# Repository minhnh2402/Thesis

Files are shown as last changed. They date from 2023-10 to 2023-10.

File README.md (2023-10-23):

# THIẾT KẾ VÀ ĐIỀU KHIỂN ROBOT DELTA CỘNG TÁC VỚI CON NGƯỜI

- [THIẾT KẾ VÀ ĐIỀU KHIỂN ROBOT DELTA CỘNG TÁC VỚI CON NGƯỜI](#thiết-kế-và-điều-khiển-robot-delta-cộng-tác-với-con-người)
  - [1. Mục tiêu đồ án](#1-mục-tiêu-đồ-án)
  - [2. Thiết kế cơ khí](#2-thiết-kế-cơ-khí)
  - [3. Thiết kế hệ thống điện](#3-thiết-kế-hệ-thống-điện)
  - [4. Mô hình hoá và thiết kế bộ điều khiển](#4-mô-hình-hoá-và-thiết-kế-bộ-điều-khiển)
  - [5. Xây dựng chương trình điều khiển Robot](#5-xây-dựng-chương-trình-điều-khiển-robot)
    - [5.1. Điều khiển robot thông qua mạng RTEX](#51-điều-khiển-robot-thông-qua-mạng-rtex)
    - [5.2. Khung dữ liệu trong mạng](#52-khung-dữ-liệu-trong-mạng)
    - [5.3. Xây dựng chương trình chạy Robot trên Ubuntu](#53-xây-dựng-chương-trình-chạy-robot-trên-ubuntu)
    - [5.4. Giao diện điều khiển](#54-giao-diện-điều-khiển)
  - [6. Thực nghiệm](#6-thực-nghiệm)

## 1. Mục tiêu đồ án

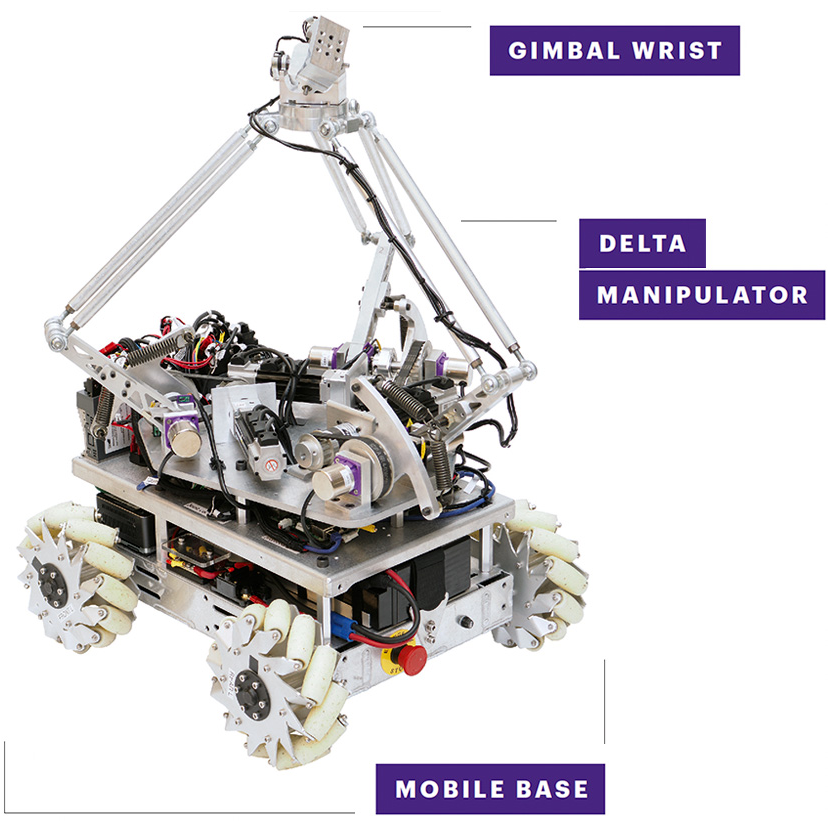
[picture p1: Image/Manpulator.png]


Đồ án hướng tới việc xây dựng cánh tay robot cho Delta Manipulator. Robot có khả năng trợ lực giúp con người nâng vật nặng từ điểm bắt đầu đến điểm kết thúc. Con người sẽ điều hướng cho robot thông qua tương tác vật lý.

## 2. Thiết kế cơ khí
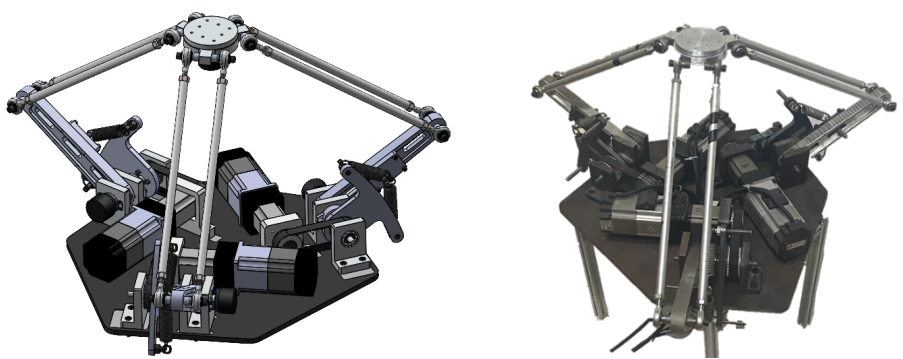
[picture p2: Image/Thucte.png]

Mô hình robot được xây dựng sau khi tính toán, thiết kế và gia công. Robot chịu tải được 10kg và sử dụng cơ cấu Series Elastic Actuator để tiếp nhận lực (Sử dụng phần mềm Solidworks và các phương pháp gia công cơ khí để xây dựng robot). 

## 3. Thiết kế hệ thống điện

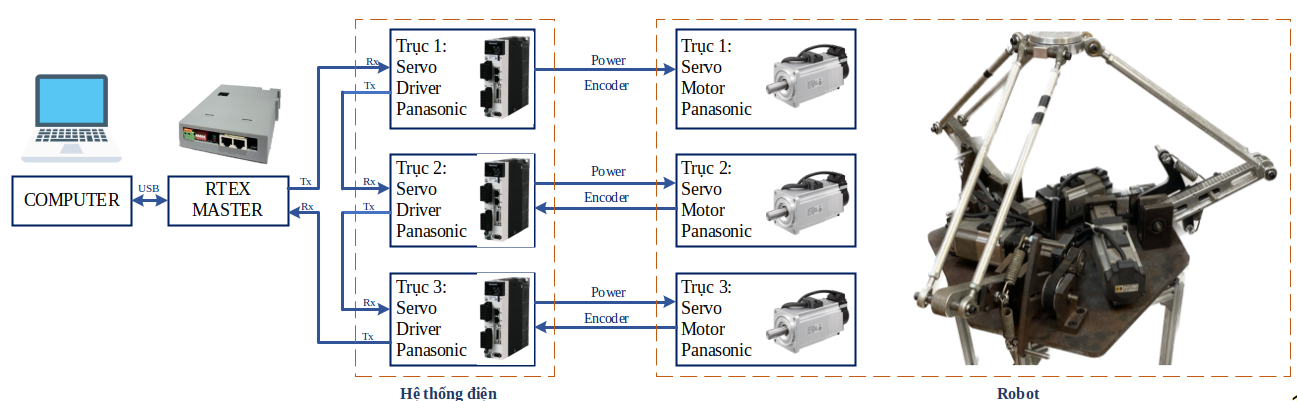
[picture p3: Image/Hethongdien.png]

Bộ điều khiển chính
- Computer: đóng vai trò là bộ điều khiển chính của hệ thống, điều khiển phân cấp đến controller là RTEX Master Board
- RTEX Master: điều khiển ba bộ AC Servo thông qua mạng RTEX

Bộ khuếch đại: Gồm ba Driver điều khiển động cơ

Động cơ: gồm 3 AC Servo Motor tương ứng với ba khớp tay máy

## 4. Mô hình hoá và thiết kế bộ điều khiển
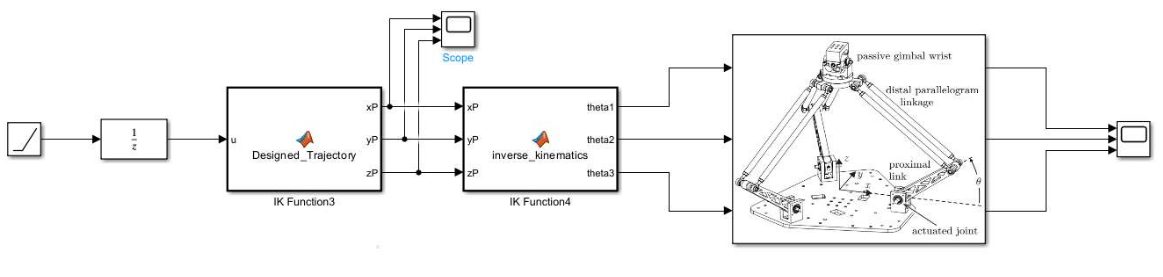
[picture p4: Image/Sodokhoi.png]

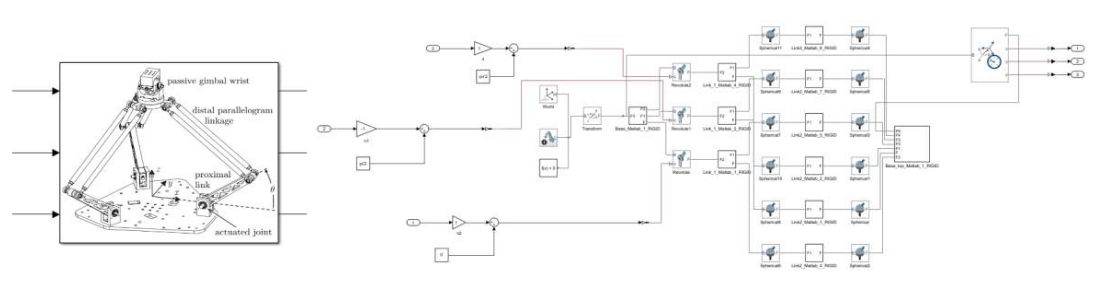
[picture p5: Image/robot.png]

Giải bài toán động học cho robot để giải quyết bài toán điều khiển. Sử dụng Matlab Simulink để mô hình hoá và kiểm tra thuật toán.
Robot sử dụng thuật toán Point to point để bám quỹ đạo và ứng dụng thuật toán Admitance Control cho bài toán tương tác với con người.
example
## 5. Xây dựng chương trình điều khiển Robot
### 5.1. Điều khiển robot thông qua mạng RTEX
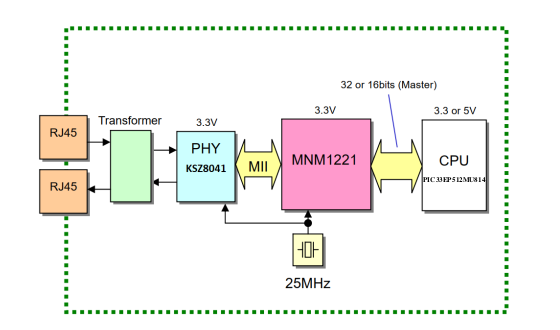
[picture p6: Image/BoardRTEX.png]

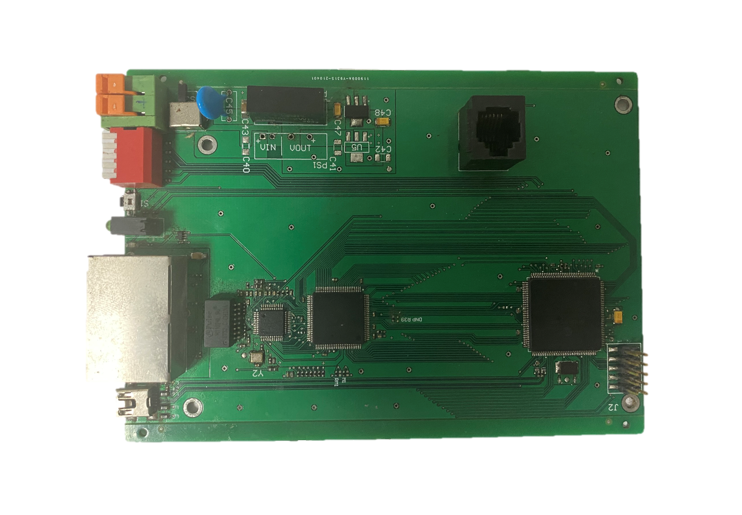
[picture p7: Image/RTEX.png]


Sơ đồ tổng quan mạch gồm ba khối chính:
- PIC33EP521MU814: vi điều khiển trung tâm của board
- MNM1221: RTEX Protocol IC, đóng vai trò giao thức kết nối mạng RTEX
- KSZ8041: PHY(Physical Layer Chip), tạo lớp vật lý đóng vai trò truyền nhận dữ liệu.

### 5.2. Khung dữ liệu trong mạng
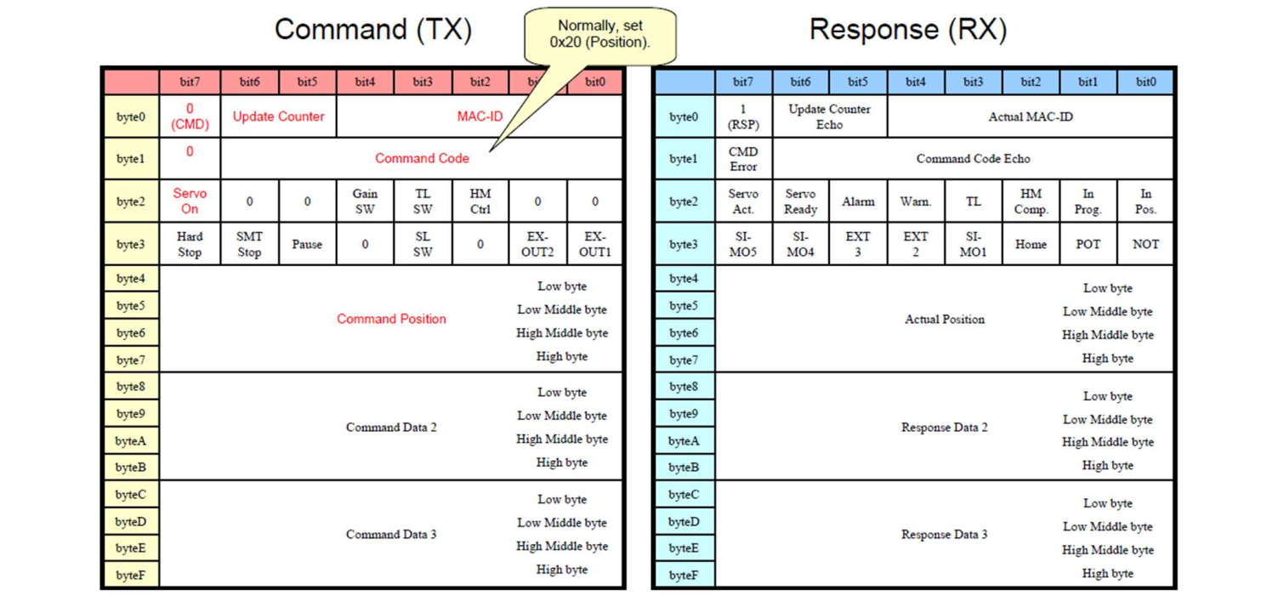
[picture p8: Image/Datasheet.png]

Đọc Datasheet của MNM1221 để thiết lập các cấu hình và chức nằng cũng như mode chạy AC Servo PANASONIC.

### 5.3. Xây dựng chương trình chạy Robot trên Ubuntu

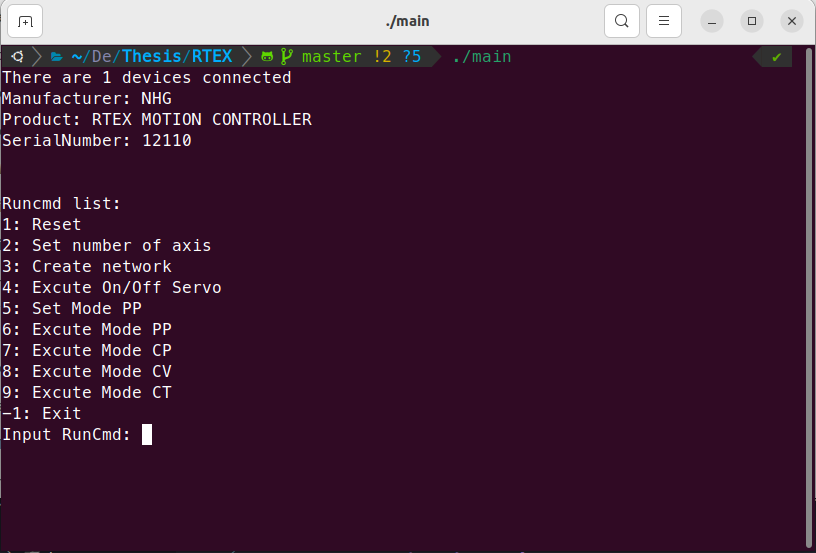
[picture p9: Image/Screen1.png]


Xây dựng chương trình điều khiển Robot chạy trên nền tảng Ubuntu, sử dụng giao thức USB HID để điều khiển RTEX Board. Dùng để test chương trình điều khiển, chương trình có sử dụng thread khác nhau để có thể điều khiển và đọc dữ liệu.

### 5.4. Giao diện điều khiển
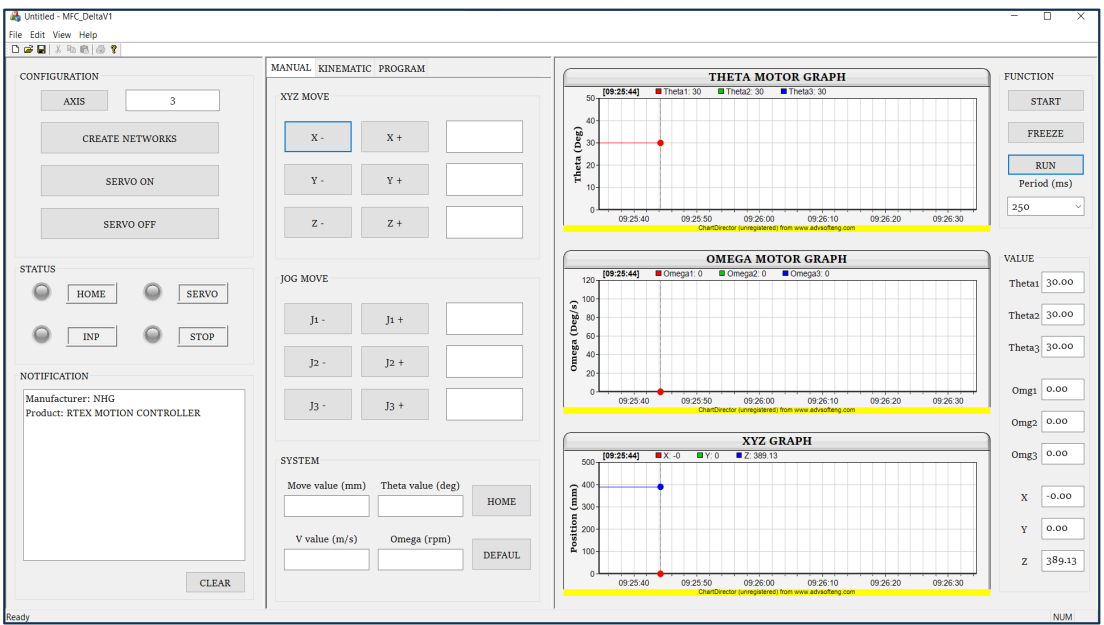
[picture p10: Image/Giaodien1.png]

Xây dựng giao diện điều khiển trên MFC, giao diện có các chức năng điều khiển robot cũng như lấy các giá trị được trả về từ encoder, thiết lập quỹ đạo cho Robot.

## 6. Thực nghiệm
Kết quả thực nghiệm sai số về mặt vị trí theo thời gian khi robot bám theo quỹ đạo hình tròn trong mặt phẳng OXY

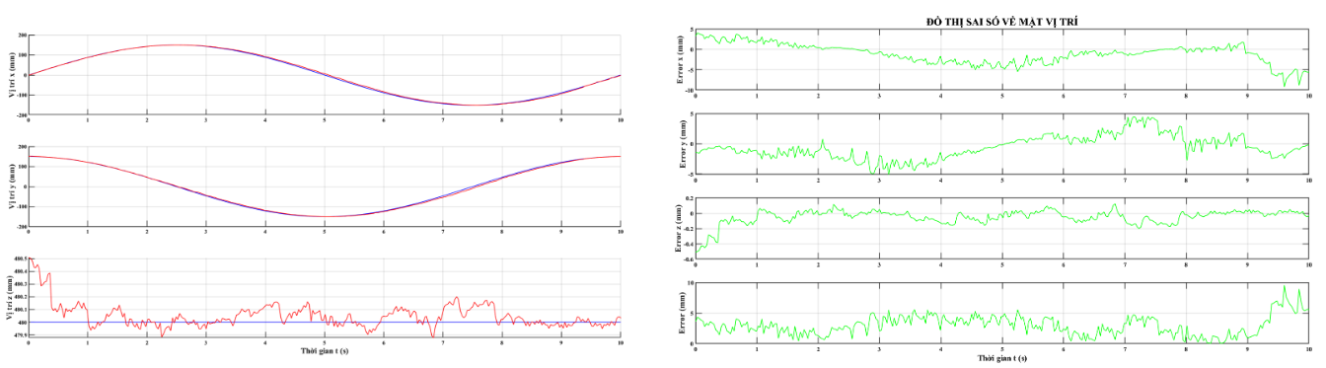
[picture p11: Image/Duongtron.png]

Kết quả thực nghiệm sai số về mặt vị trí theo thời gian khi robot bám theo quỹ đạo hình tròn trong mặt phẳng 

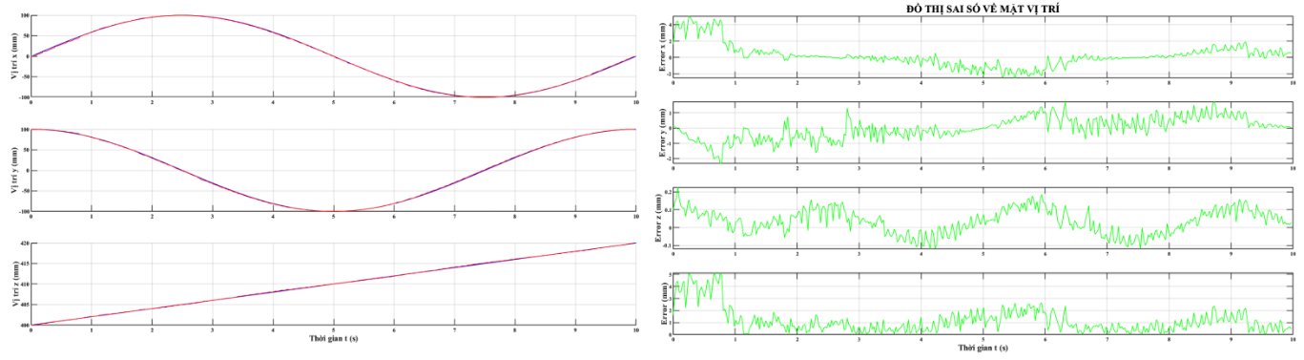
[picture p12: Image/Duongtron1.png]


[Link thực nghiệm bám quỹ đạo hình tròn](https://www.youtube.com/watch?v=yH_MfY3dLOM)

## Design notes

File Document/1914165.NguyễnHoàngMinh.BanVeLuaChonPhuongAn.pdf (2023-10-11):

THIẾT KẾ ROBOT DELTA TƯƠNG TÁC VỚI CON NGƯỜI MỤC TIÊU Thiết kế tay robot với các yêu cầu sau: - | Cơ cấu linh hoạt - | Chịu được tải trọng 10 kg - | Trọng lượng robot nhẹ LỰA CHỌN KẾT CẤU TAY ROBOT Ưu điểm: - | Không gian làm việc lớn - | Khả năng mô phỏng chuyển động của con người Nhược điểm - | Khả năng chịu tải thấp - | Khả năng ổn đinh thấp - | Độ chính xác thấp Ưu điểm: - | Tính ổn định cao - | Khả năng chịu tải tốt - | Độ chính xác cao Nhược điểm - | Không gian làm việc nhỏ - | Độ chính xác thấp LIÊN KẾT NỐI TIẾP LIÊN KẾT SONG SONG | PHƯƠNG ÁN ĐIỆN - ĐIỀU KHIỂN Ưu điểm: - | Giá thành trung bình - | Tính tùy biến cao - | Có đầy đủ chức năng điều khiển và giao tiếp Nhược điểm - | Chống nhiễu kém - | Tự xây dựng các chức năng liên quan đến motion control Ưu điểm: - | Dễ dàng lập trình - | Chống nhiễu tốt Nhược điểm - | Giá thành cao - | Tốc độ phát xung thấp - | Khả năng tùy biến kém - | Ứng dụng lập trình cho robot phức tạp VI ĐIỀU KHIỂN BỘ ĐIỀU KHIỂN PLC 1 | PHƯƠNG ÁN CƠ KHÍ Ưu điểm: - | Độ chính xác cao - | Momen xoắn lớn Nhược điểm - | Giá thành cao Ưu điểm: - | Tương đối chính xác - | Giá thành thấp Nhược điểm - | Tốc độ bị giới hạn - | Dễ xảy ra hiện tượng trượt bước - | Momen xoắn giảm theo tốc độ ĐỘNG CƠ AC SERVO ĐỘNG CƠ BƯỚC 2 | Ưu điểm: - | Tương đối chính xác - | Giá thành thấp Nhược điểm - | Momen xoắn thấp - | Gây tiếng ồn ĐỘNG CƠ DC SERVO Dựa vào mục tiêu đề bài, thiết kế cánh tay cho mobile manpulator, cánh tay cần có khối lượng nhẹ, linh hoạt, và tỉ lệ giữa tải trọng và khả năng chịu tải lớn, ta chọn thiết kế cánh tay robot theo dạng liên kết song song | Sau khi phân tích ba phương án, ta lựa chọn phương án sử dụng AC Servo, do yêu cầu cánh tay chịu được tải trọng, có độ chính xác và lab hiện đang sẳn có | 123 123 | LỰA CHỌN ĐỘNG CƠ | Chọn động cơ Trục 1: Motor: 200W MHMD022G1V Panasonic Driver: MADHT1507NB4 Chọn động cơ Trục 2: Motor: 200W MHMD022G1V Panasonic Driver: MADHT1507NB4 Chọn động cơ Trục 3: Motor: 200W MHMD022G1V Panasonic Driver: MADHT1507NB4 | Chức năng | Họ và tên | Chữ ký | Ngày Thiết kế Hướng dẫn Duyệt | Nguyễn H Minh PGS.TS N.H.Q ThịnhĐỒ ÁN TỐT NGHIỆP | Số lượng | Khối lượng | Tỷ lệ 1 | 1:1 Tờ 1 | Số tờ : 1 Trường Đại học Bách Khoa TP.HCM BẢN VẼ LỰA CHỌN PHƯƠNG ÁN Ưu điểm: - | Hỗ trợ nhiều motion profile - | Điều khiển đồng bộ, thời gian thực - | Kết nối đơn giản hiệu quả Nhược điểm - | Chi phí cao - | Phải lựa chọn đúng dòng AC SERVO RTEX MASTER Sau khi phân tích ba phương án, ta lựa chọn phương án sử dụng RTEX Motion, lab hiện đang sẳn có | PGS.TS N.D Anh

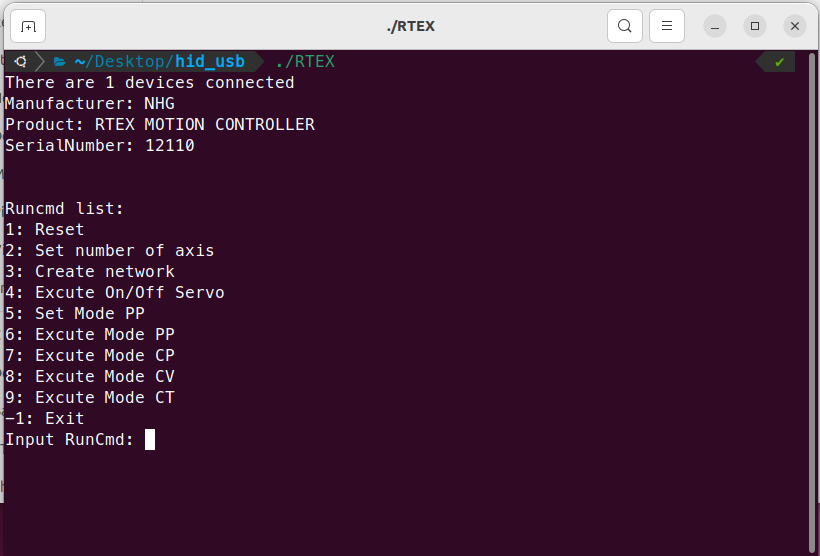
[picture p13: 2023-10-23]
Image/Screen.png

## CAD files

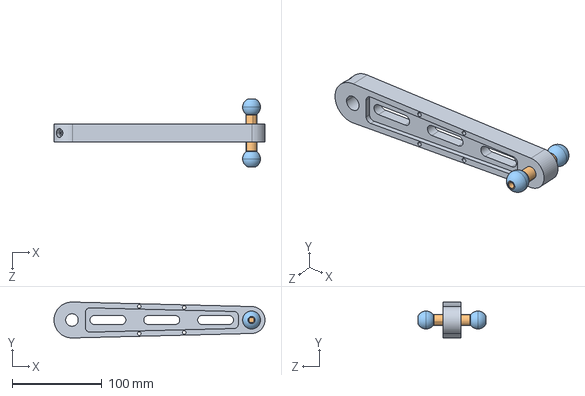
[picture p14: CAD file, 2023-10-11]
Matlab_Delta/Link_1_Matlab_Default_sldprt.STEP
235.0 x 40.0 x 76.0 mm

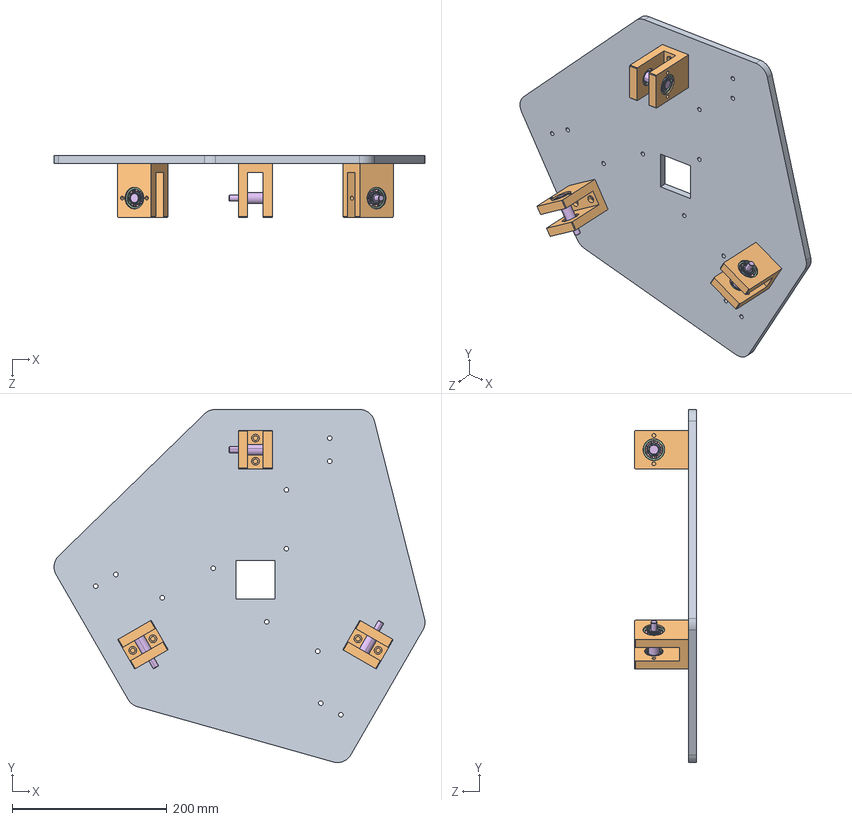
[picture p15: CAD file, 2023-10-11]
Matlab_Delta/Base_Matlab_Default_sldprt.STEP
479.6 x 456.4 x 80.0 mm

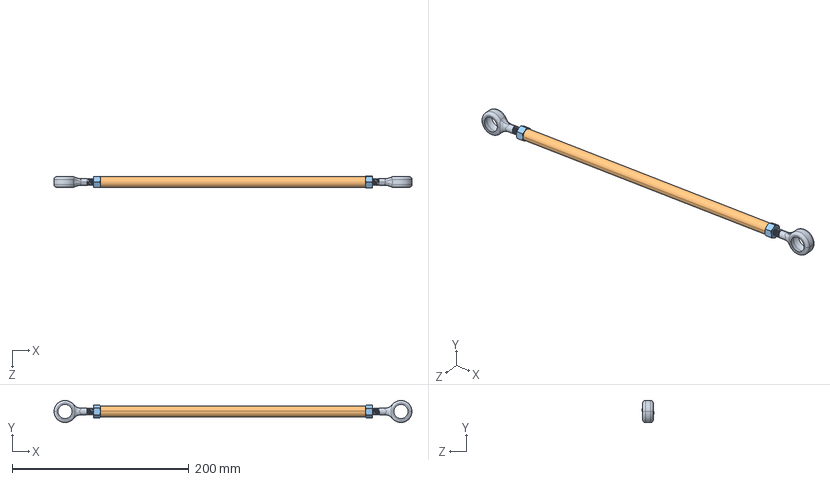
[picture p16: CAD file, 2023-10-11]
Matlab_Delta/Link2_Matlab_Default_sldprt.STEP
405.0 x 25.0 x 13.2 mm

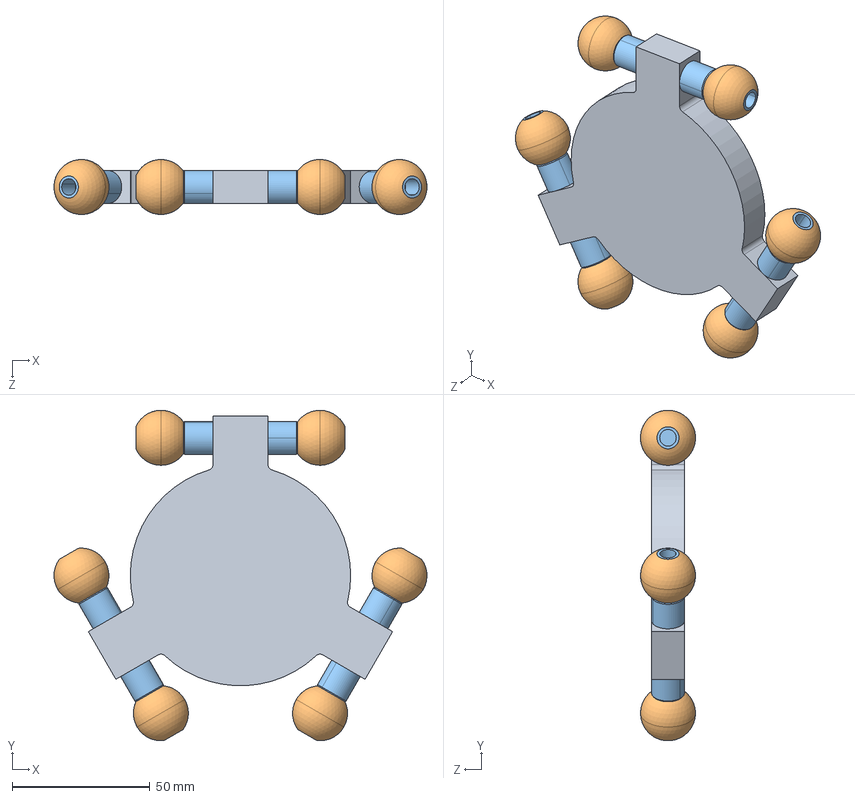
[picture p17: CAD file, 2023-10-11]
Matlab_Delta/Base_top_Matlab_Default_sldprt.STEP
135.4 x 120.0 x 20.0 mm

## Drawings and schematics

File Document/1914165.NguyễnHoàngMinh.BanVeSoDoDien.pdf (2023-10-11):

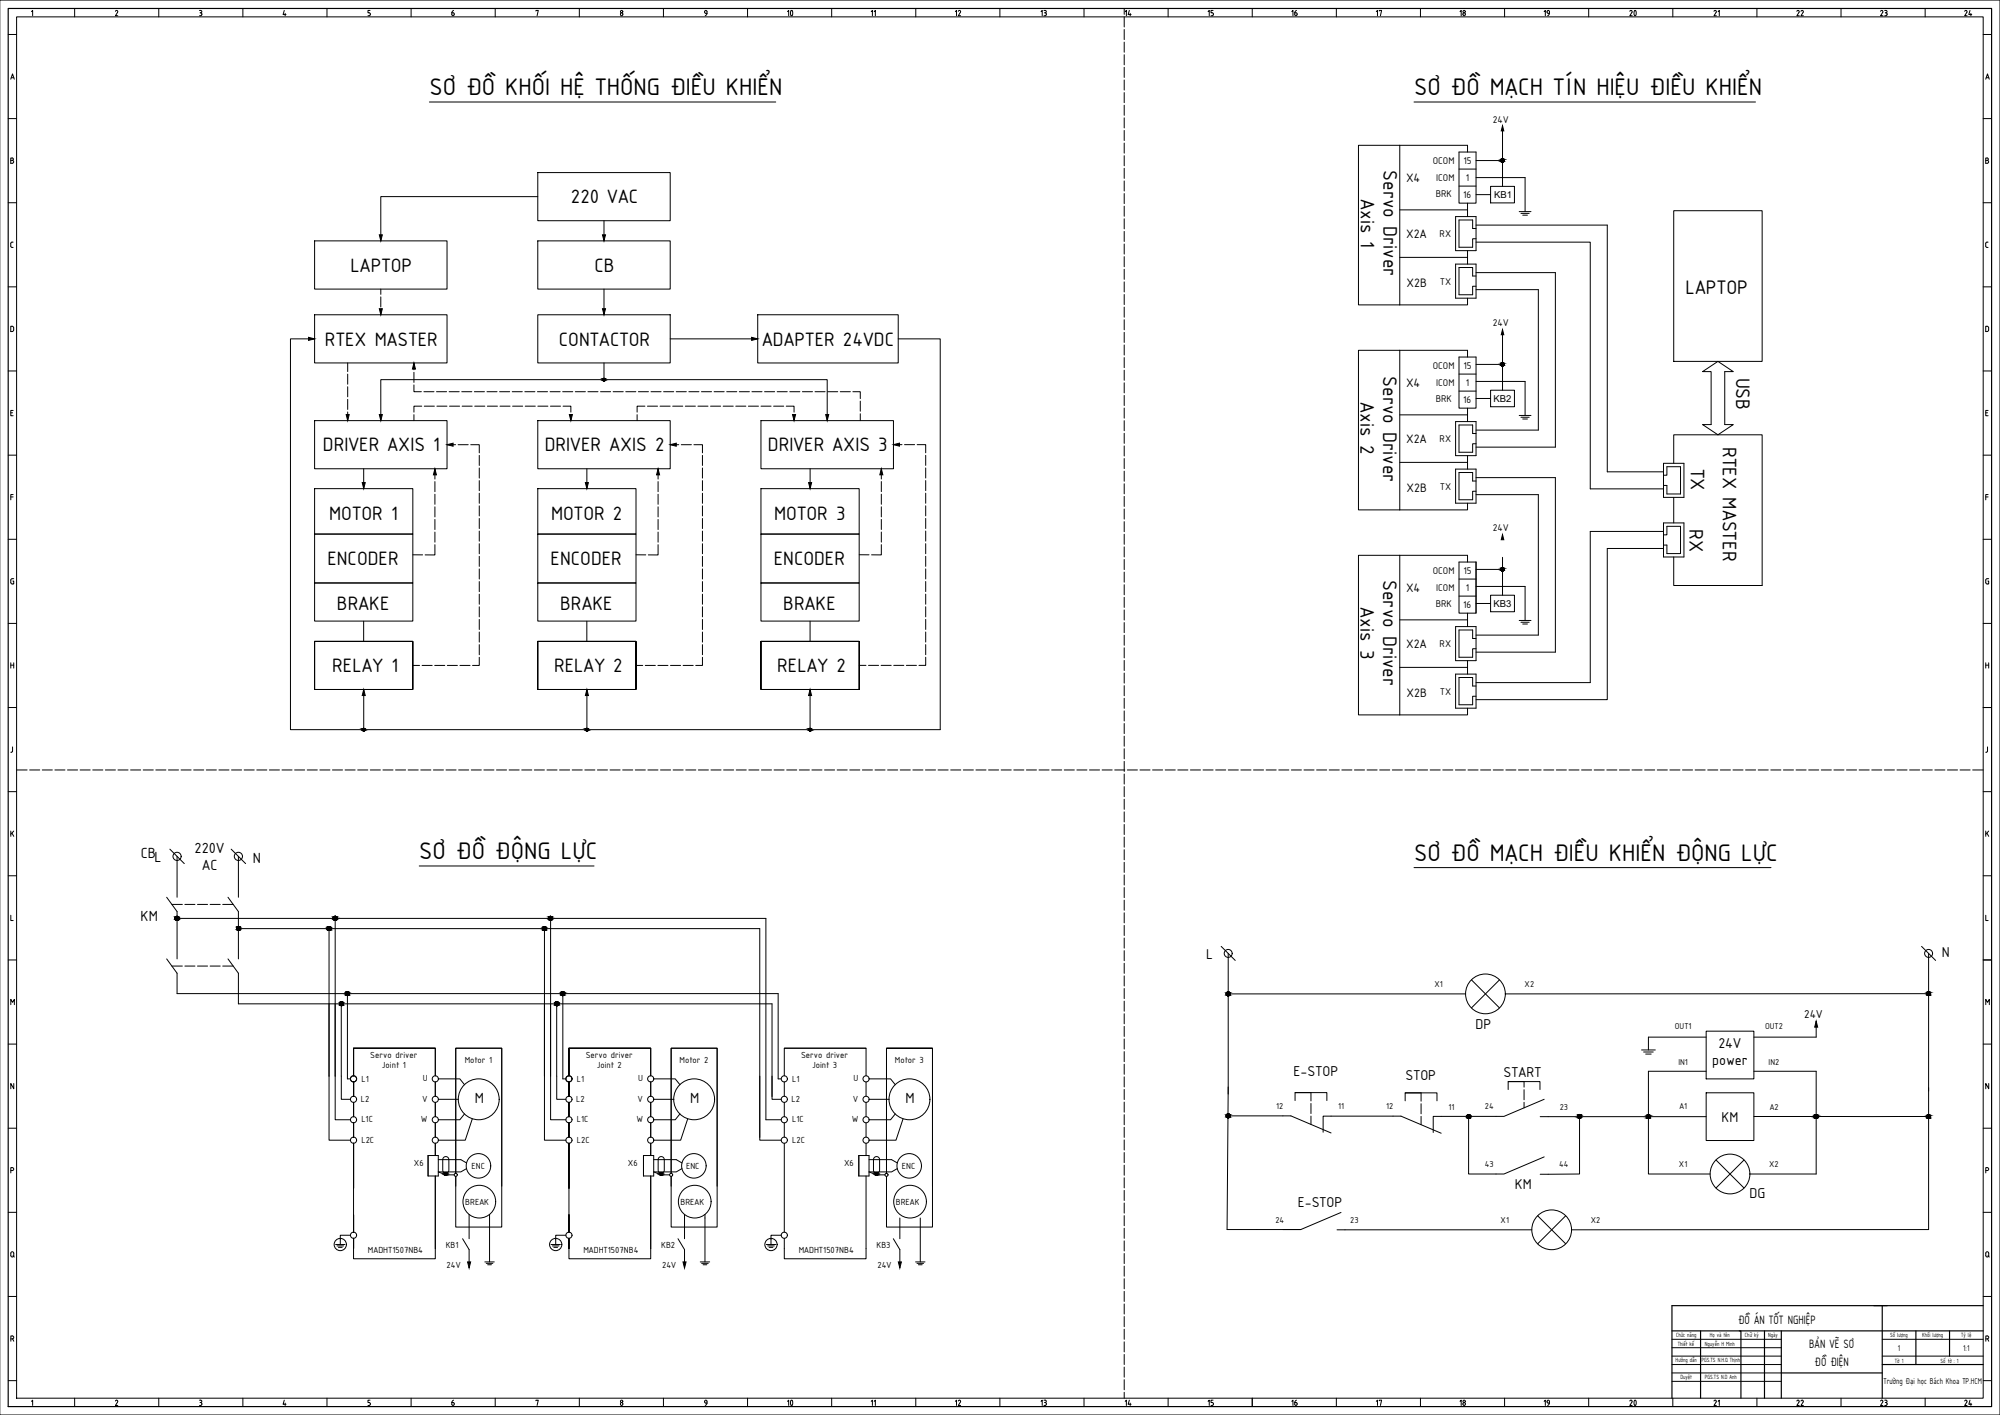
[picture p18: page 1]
MENC CBKM; Servo driver Joint 3; Motor 3 L1 L2L1C L2C; UVW MENC BREAK Servo driver Joint 1 MADHT1507NB4; Motor 1 L1 L2L1C L2C; UVW; MENC BREAK Servo driver Joint 2; Motor 2 L1 L2L1C L2C; UVW 24V KB1; X6 MADHT1507NB4; MADHT1507NB4; N KM KM E-STOP; STOP; START; DG E-STOP 24; 24V power OUT1; OUT2; IN2 BREAK 24V KB3 220 VAC LAPTOP RTEX MASTER DRIVER AXIS 1; CONTACTOR CB; ADAPTER 24VDC DRIVER AXIS 2; DRIVER AXIS 3 MOTOR 1; MOTOR 2; MOTOR 3 ENCODER BRAKE RELAY 1; ENCODER BRAKE RELAY 2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

USB Chức năng Họ và tên Chữ ký Ngày Thiết kế Hướng dẫn Duyệt Nguyễn H Minh PGS.TS N.H.Q ThịnhĐỒ ÁN TỐT NGHIỆP Số lượng Khối lượng Tỷ lệ 1 1:1 Tờ 1 Số tờ : 1 Trường Đại học Bách Khoa TP.HCM BẢN VẼ SƠ ĐỒ ĐIỆN SƠ ĐỒ KHỐI HỆ THỐNG ĐIU KHIN SƠ ĐỒ MCH TÆN HIỆU ĐIU KHIN SƠ ĐỒ ĐNG LC SƠ ĐỒ MCH ĐIU KHIN ĐNG LC PGS.TS N.D Anh

Axis 1 X4 151 OCOM ICOM BRK 16 X2A X2B RXTX

Axis 2 X4 151 OCOM ICOM BRK 16 X2A X2B RXTX

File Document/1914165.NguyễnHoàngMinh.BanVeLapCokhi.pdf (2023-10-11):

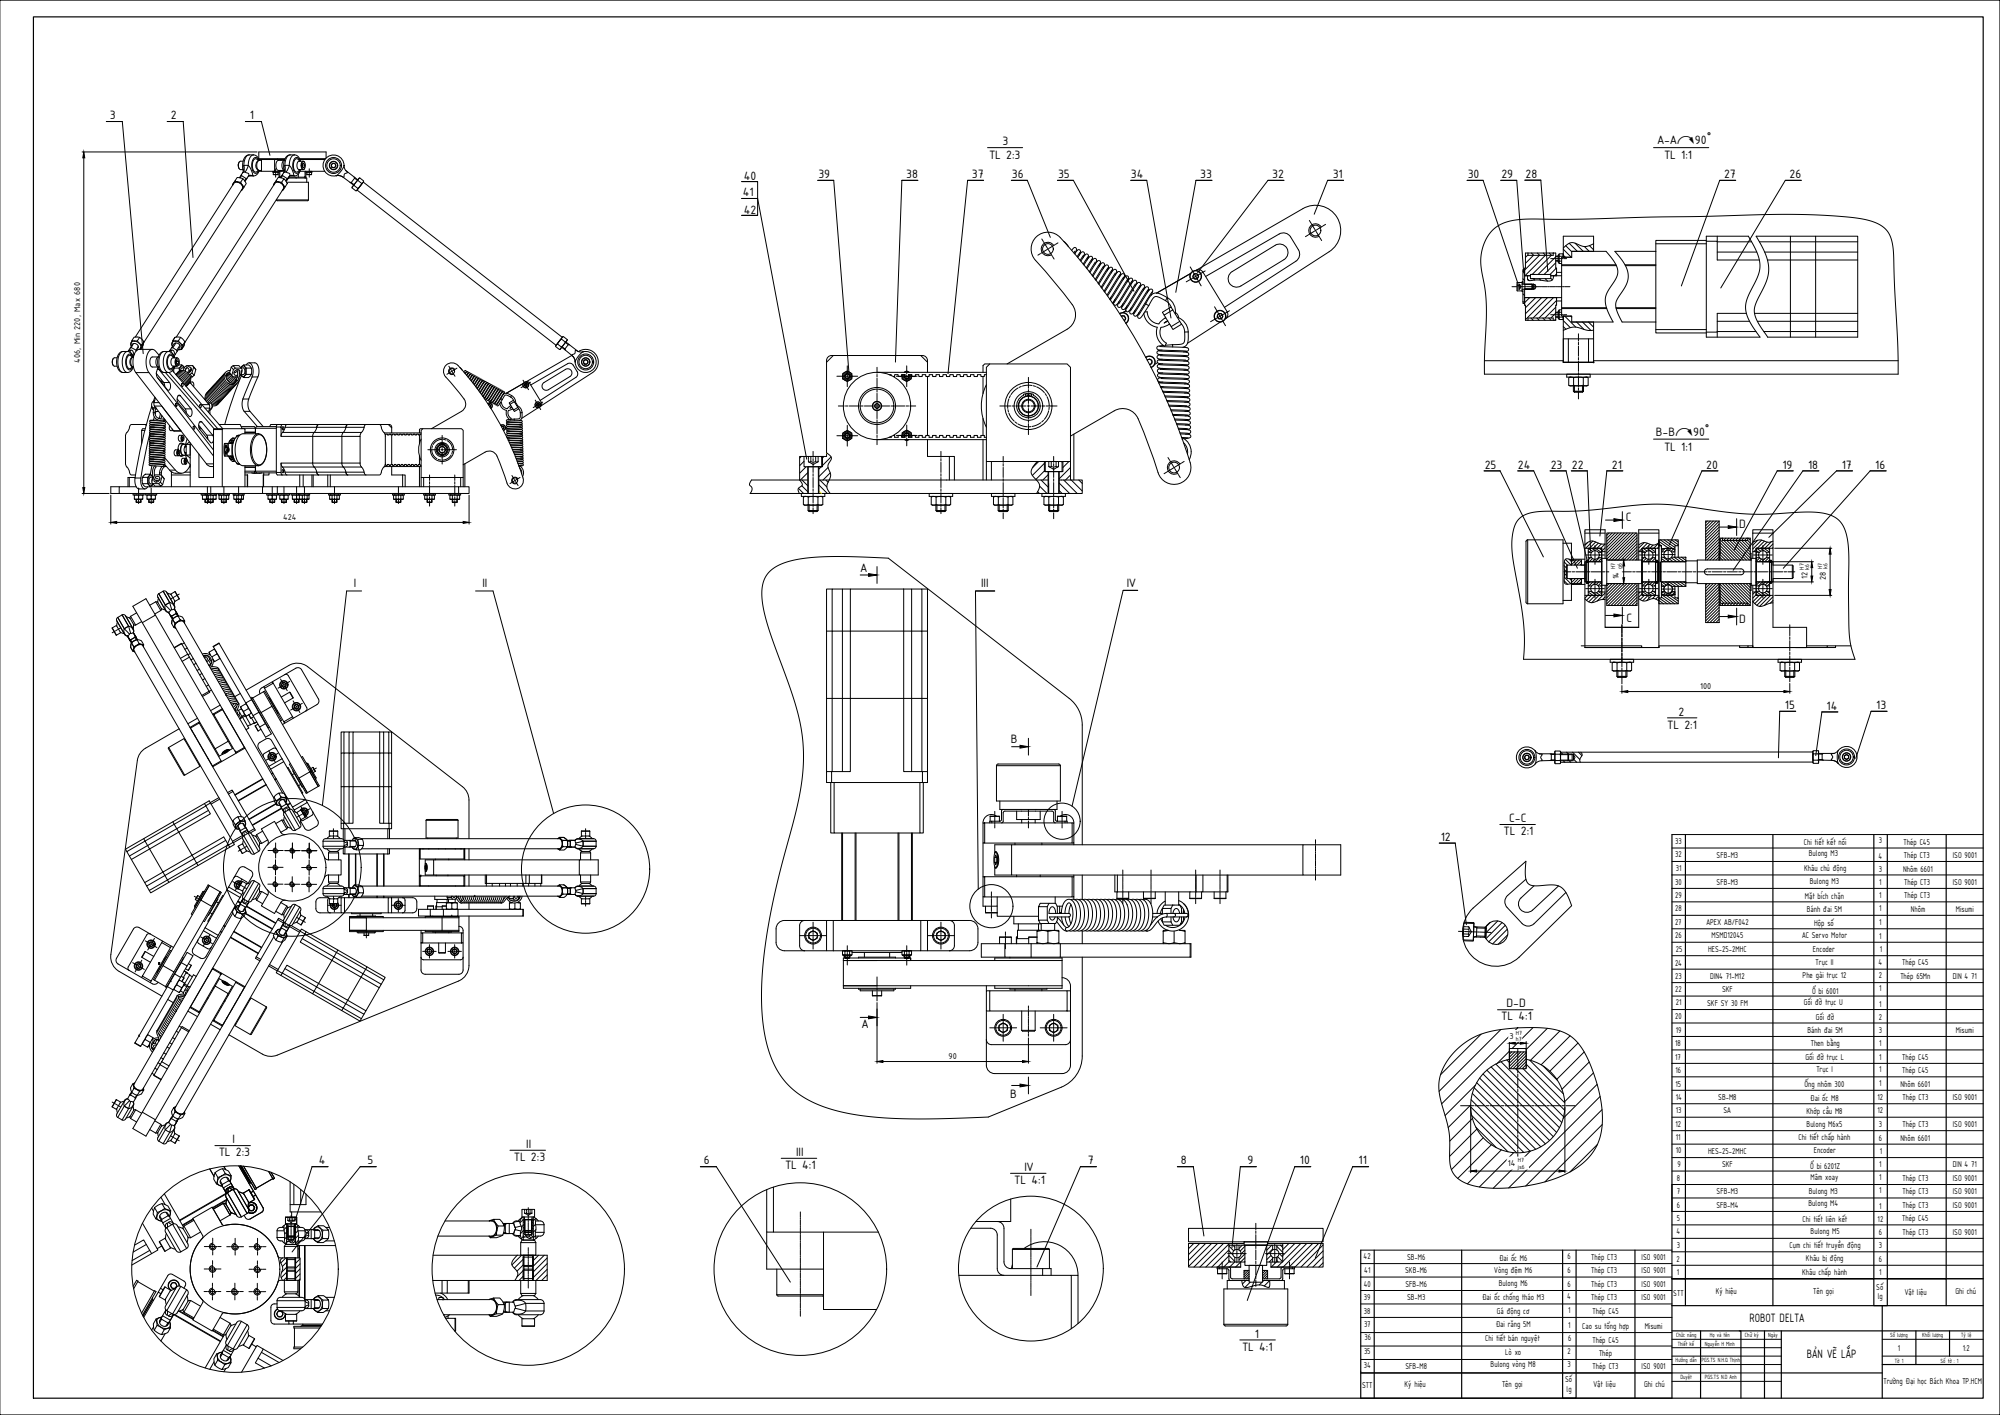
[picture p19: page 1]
III; Chức năng; Họ và tên; Chữ ký; Ngày Thiết kế Hướng dẫn Duyệt; Nguyễn H Minh PGS.TS N.H.Q Thịnh; ROBOT DELTA; Số lượng; Khối lượng; Số tờ : 1 Trường Đại học Bách Khoa TP.HCM BẢN VẼ LẮP 123456789101112131415 STT; Tên gọi; Sốlg Ký hiệu 16 TL 1:1 TL 1:1 CC C-C; 1361211111631212116 Khâu chấp hành Cụm chi tiết truyền động Bulong M5 Chi tiết liên kết Bulong M4 Bulong M3 Mâm xoay Encoder Chi tiết chấp hành Bulong M6x5 Khớp cầu M8 Đai ốc M8 Ống nhôm 300 Trục I Khâu bị động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

406, Min 220, Max 680 4 5 8 9 10 11STT Tên gọi Sốlg Ký hiệu Vật liệu Ghi chú 34353637383940 3261146 Bulong vòng M8 Chi tiết bán nguyệt Đai răng 5M Gá động cơ Đai ốc chống tháo M3 Bulong M6 Lò xo 41 Vòng đệm M6 6 42 Đai ốc M6 6 31 3233 343 Khâu chủ động Bulong M3 Chi tiết kết nối I II I TL 2:3 II TL 2:3 III TL 4:1 IV TL 4:1 1 TL 4:1 2 TL 2:1 3 TL 2:3 15 14 13 SFB-M8 SFB-M3 Thép CT3 ISO 9001 Thép CT3 Thép CT3 Thép CT3 Thép CT3 Thép CT3 ISO 9001 ISO 9001 ISO 9001 ISO 9001 SKB-M6 SFB-M6 SB-M6 SB-M3 HES-25-2MHC DIN4 71-M12 Thép 65Mn DIN 4 71 Thép CT3 Thép CT3 ISO 9001 ISO 9001 SFB-M4 SFB-M3 APEX AB/F042 MSMD12045 SFB-M3 Thép CT3 ISO 9001 Cao su tổng hợp Misumi Thép Nhôm DIN 4 71 ISO 9001 Thép C45 Thép CT3 Thép CT3 Thép CT3 Thép CT3 ISO 9001 ISO 9001 ISO 9001 ISO 9001 SKF SKF Ổ bi 6201Z Nhôm 6601 SA HES-25-2MHC Nhôm 6601 SB-M8 Thép C45 Thép C45 Thép C45 Thép C45 Nhôm 6601 Thép C45 Thép C45 Misumi SKF SY 30 FM Thép CT3 Misumi A-A↷90˚ B-B↷90˚ AA BB 90

k6 100 14 H7 js6 3 H7 h7 PGS.TS N.D Anh

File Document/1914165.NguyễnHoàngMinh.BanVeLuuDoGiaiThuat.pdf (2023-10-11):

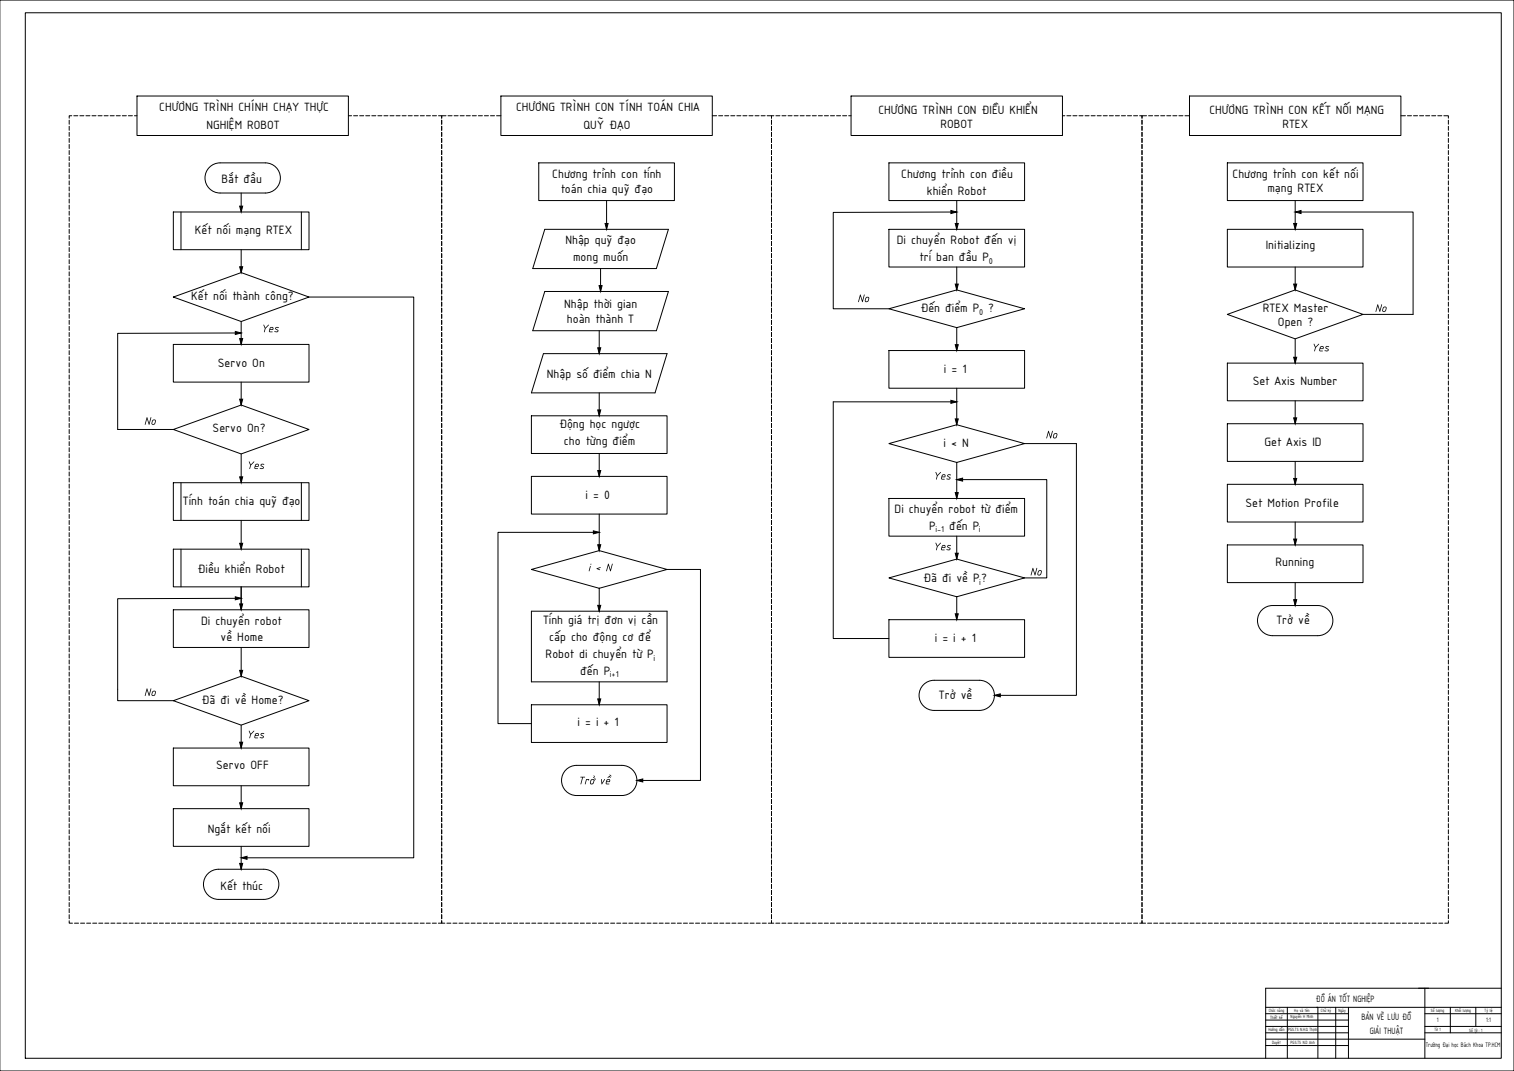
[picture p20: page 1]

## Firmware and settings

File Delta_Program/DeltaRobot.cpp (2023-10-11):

#include "DeltaRobot.h"
#include <cmath>
#include <fstream>


Delta::Delta() {
	// Constructor for the delta class. This function allows you to create an instance of the delta class and sets some properties of the robot.
	PI = 3.14159265358979323846;
	R = 168;
	r = 50;
	d = 45;
	L = 200;
	l = 380;
	a = r - R; // -118
	b = (-sqrt(3) / 2) * (r - R);
	c = 0.5 * (R - r);
	rMax = 200;
	zMin = 253;
	zMax = 605;
}


void Delta::goHome() {
	/* Delta will go to its home position (x,y,z) = (0,0,-47.06) where all joint angles are zero. The robot will report its joint angles to the serial monitor*/
	myTheta.q1 = myTheta.q2 = myTheta.q3 = 0;
	goToAngle(myPoint, myTheta);
	reportAngles();
}

void Delta::goTo(PointStruct& point, ThetaStruct& theta) {
	/* Inputs the target position, (x,y,z). First, this function tests if the target position is in the workspace.
	 If so, it calculates the inverse kineamtics, moves the robot to that position. It not, the robot reports that it isnt in the workspace.
	 Finally, the robot reports its current joint angles.*/
	int inWorkspace = testInWorkspace(point);

	if (inWorkspace) {
		delta_calcInverse(point, theta);
		cout << theta.q1 << endl;
		cout << theta.q2 << endl;
		cout << theta.q3 << endl;
	}
	else {
		cout<< ("NOT IN WORKSPACE");
	}
	reportAngles();
}

int Delta::testInWorkspace(PointStruct& point) {
	/* inputs target x,y, and z position. Tests if the position if the position is in the current worksapce of the robot (set by rMax, zMin, and zMax.
	If the point is in the workspace, return 1, else return 0*/
	float r = sqrt(point.x * point.x + point.y * point.y);
	//  Serial.println(String(" test") + round(x) + String(" ") + round(z) + String(" ") + round(z));
	if ((r <= rMax) && (point.z <= zMax) && (point.z >= zMin)) {
		return 1;
	}
	else {
		return 0;
	}
}

void Delta::reportPosition() {
	/* Report the curent position of the robot*/
	//Serial.print("ATPOS ");
	//Serial.print(x0, 2);
	//Serial.print(" ");
	//Serial.print(y0, 2);
	//Serial.print(" ");
	//Serial.println(z0, 2);
}

void Delta::reportAngles() {
	/* Report the current position of the robot*/
	/*Serial.println(String("ATANG ") + round(t1) + String(" ") + round(t2) + String(" ") + round(t3));*/
}

void Delta::goToAngle(PointStruct& point, ThetaStruct& theta) {
	/* inputs angles angle1-3. Claculates forward kineamtics and tests if position is in the workspace. If so, the robot goes to those angles.
	 *  If not, the root reports that it is not in the workspace. Then, report the position of the robot. */


	delta_calcForward(point, theta);
	int inWorkspace = testInWorkspace(point);
	if (inWorkspace) {
		//t1 = angle1;
		//t2 = angle2;
		//t3 = angle3;
		//servo1.write(-t1 + 90);
		//servo2.write(-t2 + 90);
		//servo3.write(-t3 + 90);
		cout << theta.q1;
		cout << theta.q2;
		cout << theta.q3;
	}
	else {
		cout << ("NOT IN WORKSPACE");
	}
	reportPosition();

}



void Delta::delta_calcInverse(PointStruct& point, ThetaStruct& theta) {

	double E1 = -2 * L * (point.y + a);
	double F1 = -2 * L * (point.z - d);
	double G1 = pow(point.x, 2) + pow(point.y, 2) + pow(point.z, 2) + pow(L, 2)
		+ pow(a, 2) + pow(d, 2) + 2 * point.y * a - 2 * point.z * d - pow(l, 2);

	double E2 = L * (sqrt(3) * (point.x + b) + point.y + c);
	double F2 = -2 * L * (point.z - d);
	double G2 = pow(point.x, 2) + pow(point.y, 2) + pow(point.z, 2) + pow(L, 2)
		+ pow(b, 2) + pow(c, 2) + pow(d, 2) + 2 * point.x * b + 2 * point.y * c - 2 * point.z * d - pow(l, 2);

	double E3 = L * (-sqrt(3) * (point.x - b) + point.y + c);
	double F3 = -2 * L * (point.z - d);
	double G3 = pow(point.x, 2) + pow(point.y, 2) + pow(point.z, 2) + pow(L, 2)
		+ pow(b, 2) + pow(c, 2) + pow(d, 2) - 2 * point.x * b + 2 * point.y * c - 2 * point.z * d - pow(l, 2);

	double t11 = (-F1 + sqrt(pow(E1, 2) + pow(F1, 2) - pow(G1, 2))) / (G1 - E1);
	double t12 = (-F1 - sqrt(pow(E1, 2) + pow(F1, 2) - pow(G1, 2))) / (G1 - E1);

	double t21 = (-F2 + sqrt(pow(E2, 2) + pow(F2, 2) - pow(G2, 2))) / (G2 - E2);
	double t22 = (-F2 - sqrt(pow(E2, 2) + pow(F2, 2) - pow(G2, 2))) / (G2 - E2);

	double t31 = (-F3 + sqrt(pow(E3, 2) + pow(F3, 2) - pow(G3, 2))) / (G3 - E3);
	double t32 = (-F3 - sqrt(pow(E3, 2) + pow(F3, 2) - pow(G3, 2))) / (G3 - E3);

	theta.q1 = 2 * (double)atanf(t12) * (180 / PI);
	theta.q2 = 2 * (double)atanf(t22) * (180 / PI);
	theta.q3 = 2 * (double)atanf(t32) * (180 / PI);

}

void Delta::delta_calcForward(PointStruct& point, ThetaStruct& theta) {

	theta.q1 = theta.q1;
	theta.q2 = theta.q2;
	theta.q3 = theta.q3;

	double y1 = (-a + L * cos(theta.q1 * PI / 180));
	double z1 = L * sin(theta.q1 * PI / 180) + d;

	double y2 = -(-a + L * cos(theta.q2 * PI / 180)) * sin(30 * PI / 180);
	double x2 = y2 * tan(60 * PI / 180);
	double z2 = L * sin(theta.q2 * PI / 180) + d;

	double y3 = -(-a + L * cos(theta.q3 * PI / 180)) * sin(30 * PI / 180);
	double x3 = -y3 * tan(60 * PI / 180);
	double z3 = L * sin(theta.q3 * PI / 180) + d;

	double dnm = (y2 - y1) * x3 - (y3 - y1) * x2;
	double w1 = pow(y1, 2) + pow(z1, 2);
	double w2 = pow(x2, 2) + pow(y2, 2) + pow(z2, 2);
	double w3 = pow(x3, 2) + pow(y3, 2) + pow(z3, 2);

	double a1 = (z2 - z1) * (y3 - y1) - (z3 - z1) * (y2 - y1);
	double b1 = -((w2 - w1) * (y3 - y1) - (w3 - w1) * (y2 - y1)) / 2.0;

	double a2 = -(z2 - z1) * x3 + (z3 - z1) * x2;
	double b2 = ((w2 - w1) * x3 - (w3 - w1) * x2) / 2.0;

	double a = a1 * a1 + a2 * a2 + dnm * dnm;
	double b = 2 * (a1 * b1 + a2 * (b2 - y1 * dnm) - z1 * dnm * dnm);
	double c = (b2 - y1 * dnm) * (b2 - y1 * dnm) + b1 * b1 + dnm * dnm * (z1 * z1 - l * l);

	double d1 = pow(b, 2) - 4.0 * a * c;


	point.z = -0.5 * (b - sqrt(d1)) / a;
	point.x = (a1 * point.z + b1) / dnm;
	point.y = (a2 * point.z + b2) / dnm;
	cout << point.x << endl;
	cout << point.y << endl;
	cout << point.z << endl;

}
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
